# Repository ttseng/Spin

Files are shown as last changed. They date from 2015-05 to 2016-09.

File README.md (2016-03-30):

# Spin Turntable System

Find all the design files for building your own Spin turntable (http://spin.media.mit.edu/) here.

## Arduino

This folder contains the SoftModem library needed for the spin.ino Arduino sketch.  The spin sketch should be uploaded to the Arduino Uno running Spin.

## CAD

If you are building a turntable and have access to a laser cutter with a bed larger than 12", build the DEFAULT turntable.  If you have a smaller laser cutter that cannot cut material larger than 12", build the Modified 12-inch turntable design.  Both designs have the same exact footprint (13"), but the modified 12-inch turntable has smaller laser cut parts and has an additional set of three 3D printed feet.

Each contains three subfolders: _3D Print_, _Laser Cut_, and _Solidworks_.  Building your own Spin turntable requires laser cutting parts in 3/16" and 1/8" acrylic, which can be found in the _Laser Cut_ folder in Illustrator, Corel Draw, and DXF formats.  Additionally, you'll need to 3D print a gear (motor_gear.STL), which can be found in the _3D print_ folder.  Optionally, you can 3D print your own iOS device dock (which can be used with an iPhone 4/5/6 or iPad/iPad mini).  If you are building the modified turntable, you will also need to 3D print three feet.  

You can find all the original CAD files in the _Solidworks_ folder.

## PCB

The Eagle files and libraries for the Spin shield are located here.  You can purchase the shield directly from OSH Park: https://oshpark.com/profiles/scientiffic

## Processing

This is an optional Processing sketch for controlling the Spin turntable with your computer via a USB connection to the Uno.  You can use this to debug your turntable or to just control it without using an iOS device.

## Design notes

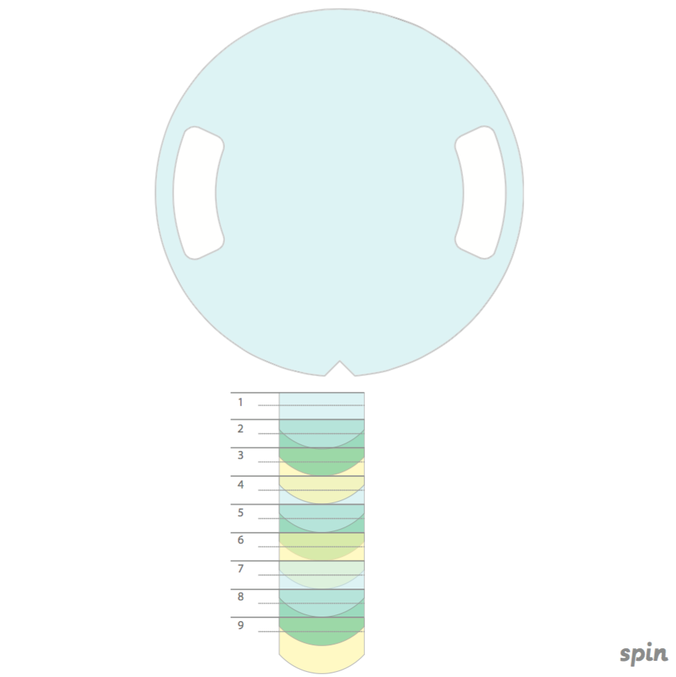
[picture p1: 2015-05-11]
Mat/mat.png

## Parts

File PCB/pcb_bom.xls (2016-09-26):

Item | Vendor | Quantity | Part Number | Total Price
Easy Drive Stepper Motor Driver | Sparkfun | 1 | ROB-12779 (https://www.sparkfun.com/products/12779) | 14.95
Blue LEDs 1206 SMD | Sparkfun | 1 (strip of 25) | PRT-12620 (https://www.sparkfun.com/products/12620) | 2.95
Male headers | Sparkfun | 2 | PRT-00116 (https://www.sparkfun.com/products/116) | 3
Female headers | Digikey | 1 | S5440-ND (http://www.digikey.com/product-detail/en/PPTC041LGBN-RC/S5440-ND/775898) | 0.63
3.5mm audio jack | Digikey | 1 | CP-43514-ND (http://www.digikey.com/product-search/en?KeyWords=CP-43514-ND&WT.z_header=search_go) | 1.18
100 Ω resistor 1206 SMD | Digikey | 4 | 311-100FRCT-ND (http://www.digikey.com/product-detail/en/0/311-100FRCT-ND) | 0.45
1 kΩ resistor 1206 SMD | Digikey | 2 | P1.0KECT-ND (http://www.digikey.com/product-detail/en/ERJ-8GEYJ102V/P1.0KECT-ND/203248) | 0.09
10 kΩ resistor 1206 SMD | Digikey | 1 | 311-10.0KFRCT-ND (http://www.digikey.com/product-detail/en/RC1206FR-0710KL/311-10.0KFRCT-ND/731430) | 0.09
0.22 µF 1206 capacitor | Digikey | 1 | 399-1251-1-ND (http://www.digikey.com/product-search/en?KeyWords=399-1251-1-ND&WT.z_header=search_go) | 0.17
 |  |  |  | Total: $23.51

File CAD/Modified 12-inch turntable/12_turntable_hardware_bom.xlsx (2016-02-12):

Item | Vendor | Quantity | Part Number | Total Price
Specialized Parts
Turntable | McMaster | 1 | 18635A52 (http://www.mcmaster.com/#18635a52/=vv6p0h) | 37.03
M3 Heat-Set Inserts | McMaster | 1 (pack of 100) | 94180A331 (http://www.mcmaster.com/#94180a331/=wy5p3e) | 12.3
Acrylic
3/16" acrylic (total area of 24" x 12") | Tap Plastics | 1 | 3/16" acrylic (http://www.tapplastics.com/product/plastics/cut_to_size_plastic/acrylic_sheets_clear/508) | 13.3
⅛" white acrylic (12"x12") | Tap Plastics | 1 | 1/8" acrylic (http://www.tapplastics.com/product/plastics/cut_to_size_plastic/acrylic_sheets_color/341) | 10
Misc Electronics
Stepper Motor | Sparkfun | 1 | ROB-09238 (https://www.sparkfun.com/products/9238) | 14.95
Arduino Uno | Sparkfun | 1 | DEV-11021 (https://www.sparkfun.com/products/11021) | 24.95
12VDC Wall Adapter | Sparkfun | 1 | TOL-09442 (https://www.sparkfun.com/products/9442) | 5.94
M3 Standoffs | Digikey | 4 | 952-2189-ND (http://www.digikey.com/product-search/en?KeyWords=952-2189-ND&WT.z_header=search_go) | 2.24
3.5mm Audio Cable | Amazon | 1 | Audio Cable (http://www.amazon.com/EMEMO®-Quality-Auxilliary-Straight-Generation/dp/B00JJVPUE2) | 5.99
Fasteners
M3 set screw (4mm length) |  | 2
M3 machine screws (10mm length) |  | 18
M3 nuts |  | 7
¼-20 machine screws (0.625" length) |  | 9
¼-20 nuts |  | 9
5/16 machine screws (2.5" length) |  | 3
5/16 nuts |  | 3
 |  |  |  | Total: $126.70 + ~ $10 for fasteners

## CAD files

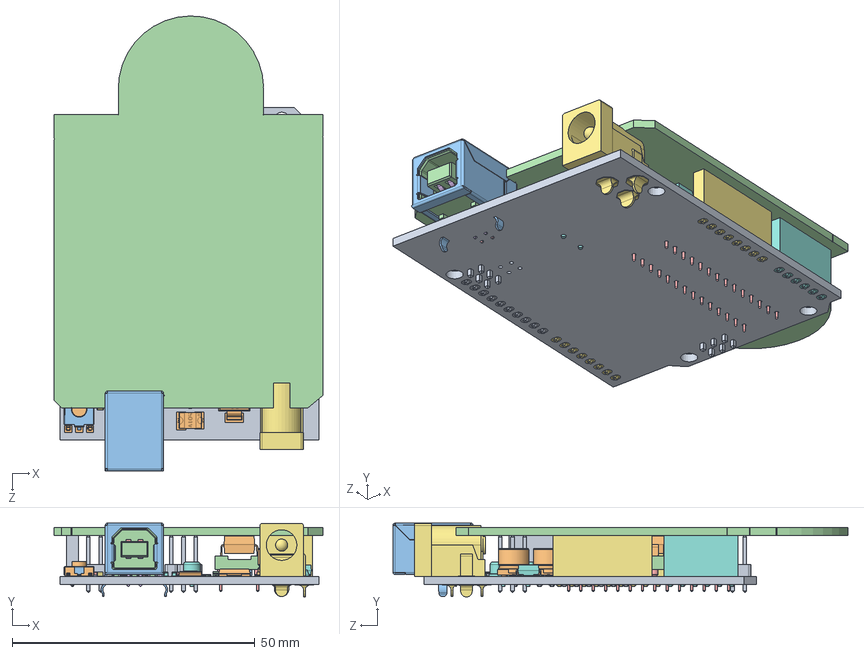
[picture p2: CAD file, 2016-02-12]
CAD/Modified 12-inch turntable/Solidworks/arduino-assembly.SLDASM
55.4 x 15.2 x 93.8 mm
unoboard blue
47uf CAP Dcase x 2
USB SHELL
USB core
usb top contact x 2
usb btm contact x 2
power jack
crystal
2pin_header__02 x 6
nano - reg
led x 4
dip28
dip socket pin x 28
atmega16u2
8 PORT HEADER x 2
6 PORT HEADER
10 PORT HEADER
ATMEL328P
102 RESISTOR PACK x 2
103 RESISTOR PACK
220 RESISTOR PACK
16mhz crystal - measured
PADS001
603 cap on pad x 8
ssot3
mf-msmf050-2
lmv358
lp2985dgkr
cd1206 diode x 2
603 resistor
blm21
m7 diode
MLC0603 x 2
RESET CORE
RESET
PCB

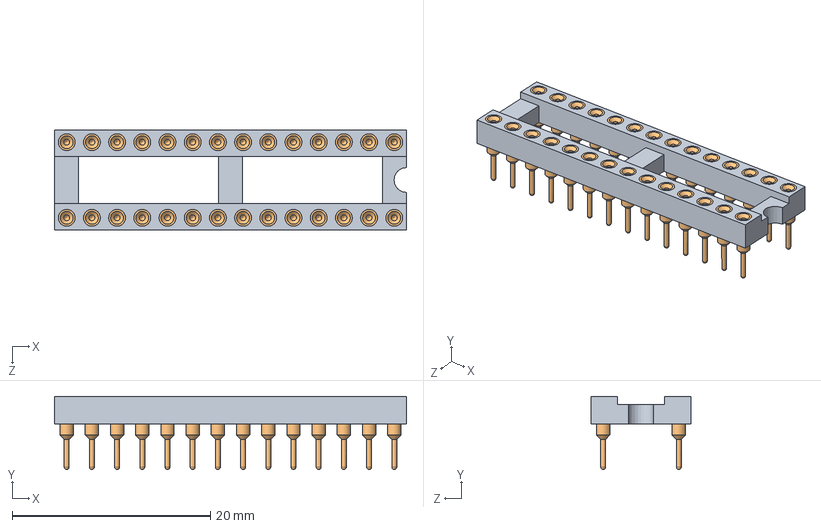
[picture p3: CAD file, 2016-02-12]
CAD/Modified 12-inch turntable/Solidworks/dip28.SLDASM
35.5 x 7.37 x 10.1 mm
dip28
dip socket pin x 28

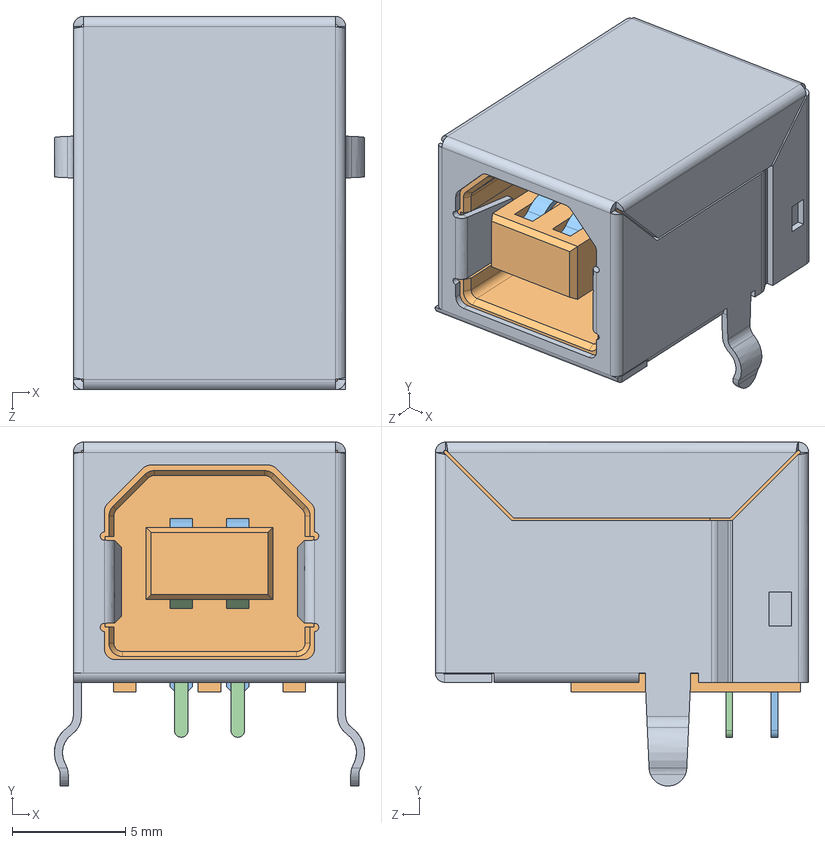
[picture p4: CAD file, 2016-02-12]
CAD/Modified 12-inch turntable/Solidworks/USB type b.SLDPRT.SLDASM
13.7 x 15.2 x 16.5 mm
USB SHELL
USB core
usb top contact x 2
usb btm contact x 2

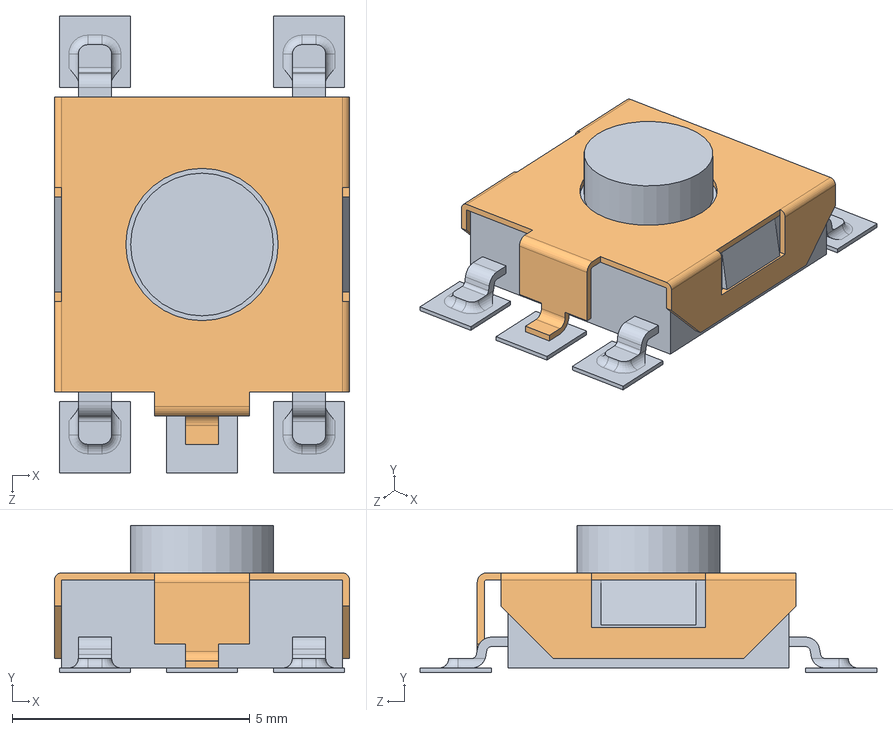
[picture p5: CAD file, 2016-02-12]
CAD/Modified 12-inch turntable/Solidworks/RESET BUTTON.SLDASM
6.20 x 3.10 x 9.60 mm
RESET CORE
RESET

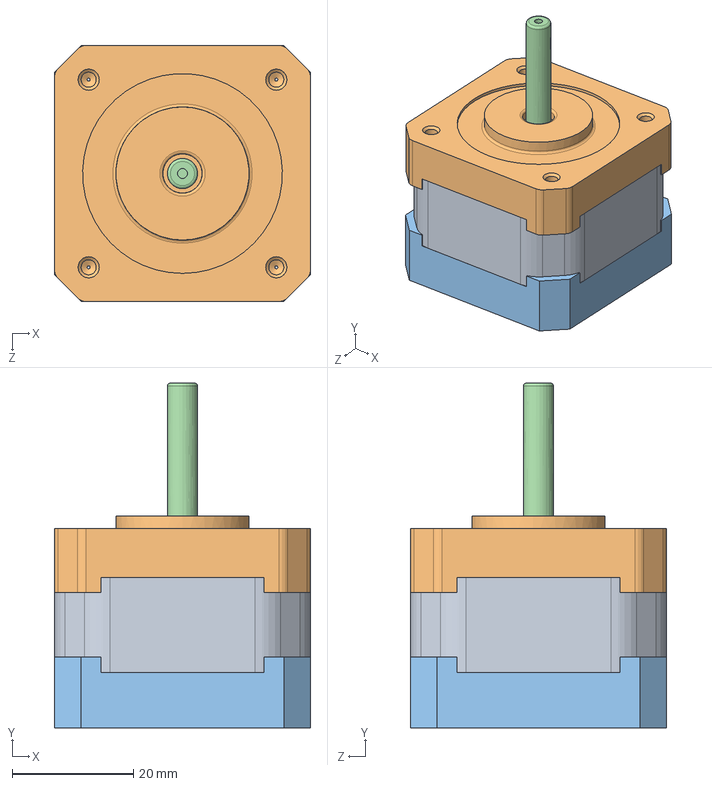
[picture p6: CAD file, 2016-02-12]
CAD/Modified 12-inch turntable/Solidworks/SparkFun Stepper Motor Assembly.SLDASM
42.3 x 57.0 x 42.3 mm
NEMA 17 Stepper Motor Middle
NEMA 17 Stepper Motor Top
NEMA 17 Stepper Motor Bottom
NEMA 17 Stepper Motor Shaft
pan cross head_am x 4

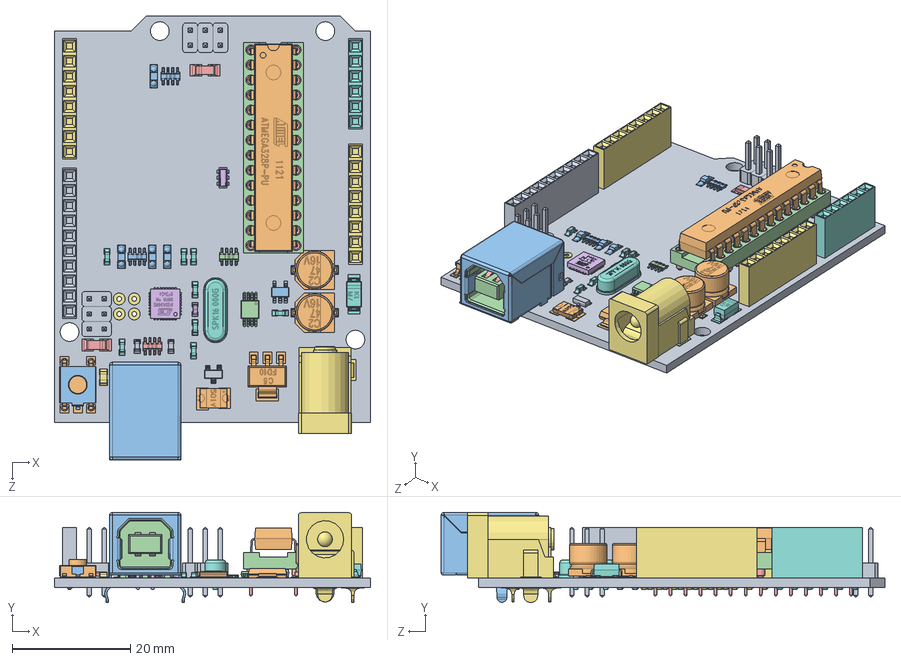
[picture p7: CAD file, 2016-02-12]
CAD/DEFAULT turntable/Solidworks/arduino uno.SLDASM
53.3 x 15.2 x 74.9 mm
unoboard blue
47uf CAP Dcase x 2
USB SHELL
USB core
usb top contact x 2
usb btm contact x 2
power jack
crystal
2pin_header__02 x 6
nano - reg
led x 4
dip28
dip socket pin x 28
atmega16u2
8 PORT HEADER x 2
6 PORT HEADER
10 PORT HEADER
ATMEL328P
102 RESISTOR PACK x 2
103 RESISTOR PACK
220 RESISTOR PACK
16mhz crystal - measured
PADS001
603 cap on pad x 8
ssot3
mf-msmf050-2
lmv358
lp2985dgkr
cd1206 diode x 2
603 resistor
blm21
m7 diode
MLC0603 x 2
RESET CORE
RESET

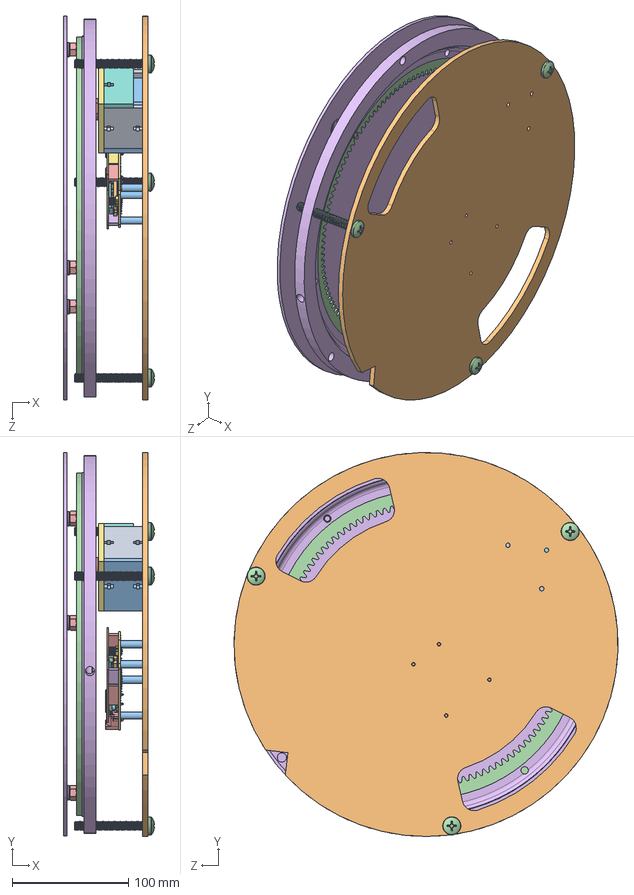
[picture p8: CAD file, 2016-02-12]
CAD/DEFAULT turntable/Solidworks/turntable_assembly.SLDASM
78.2 x 330.2 x 330.2 mm
NEMA 17 Stepper Motor Middle
NEMA 17 Stepper Motor Top
NEMA 17 Stepper Motor Bottom
NEMA 17 Stepper Motor Shaft
pan cross head_am x 4
turntable
stepper_case_top
stepper_case_side_1
stepper_case_side_2 x 2
base
stepper_case_side_3
outer_gear
motor_gear_2
unoboard blue
47uf CAP Dcase x 2
USB SHELL
USB core
usb top contact x 2
usb btm contact x 2
power jack
crystal
2pin_header__02 x 6
nano - reg
led x 4
dip28
dip socket pin x 28
atmega16u2
8 PORT HEADER x 2
6 PORT HEADER
10 PORT HEADER
ATMEL328P
102 RESISTOR PACK x 2
103 RESISTOR PACK
220 RESISTOR PACK
16mhz crystal - measured
PADS001
603 cap on pad x 8
ssot3
mf-msmf050-2
lmv358
lp2985dgkr
cd1206 diode x 2
603 resistor
blm21
m7 diode
MLC0603 x 2
RESET CORE
RESET
PCB
standoff x 4
91772A634 x 3
90499A029 x 3
94836A420 x 3

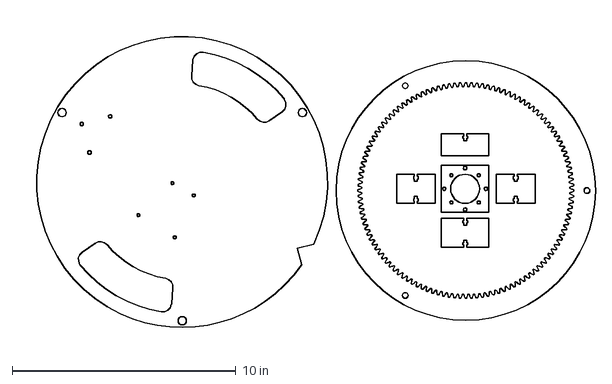
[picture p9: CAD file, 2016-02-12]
CAD/DEFAULT turntable/Laser Cut/DXF/3_16_acrylic.dxf
25.9 x 14.6 in

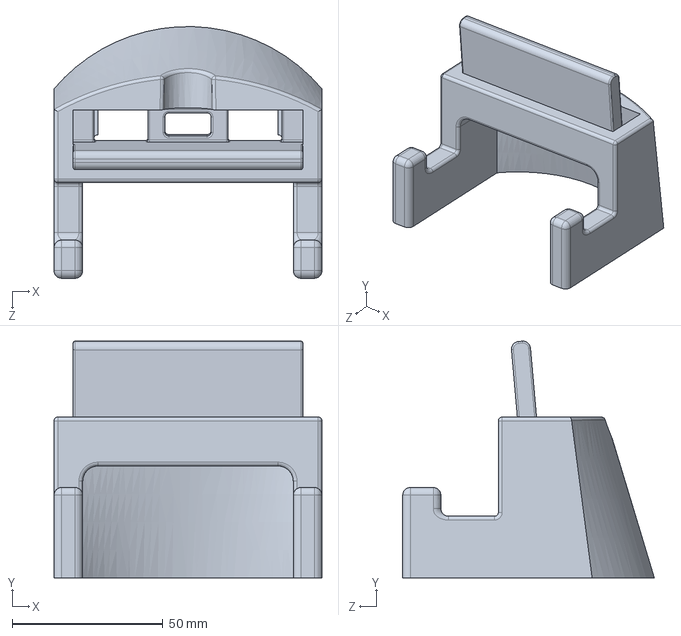
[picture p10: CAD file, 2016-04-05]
CAD/DEFAULT turntable/Solidworks/ios_dock.SLDPRT
88.9 x 78.5 x 83.5 mm

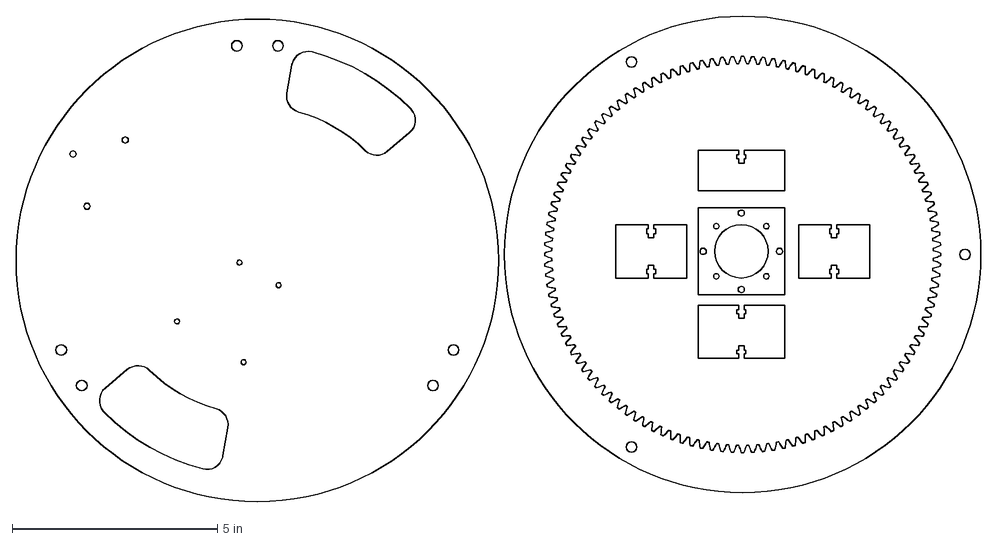
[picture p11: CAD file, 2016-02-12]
CAD/Modified 12-inch turntable/Laser Cut/DXF/3_16_acrylic.dxf
23.5 x 11.8 in

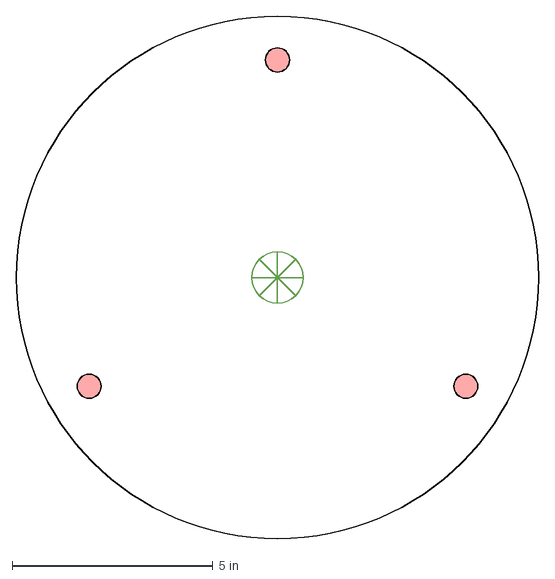
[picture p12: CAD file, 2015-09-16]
CAD/DEFAULT turntable/Laser Cut/DXF/1_8_acrylic.dxf
13.0 x 13.0 in

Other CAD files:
CAD/DEFAULT turntable/Solidworks/USB type b.SLDPRT.SLDASM
CAD/DEFAULT turntable/Solidworks/dip28.SLDASM
CAD/DEFAULT turntable/Solidworks/RESET BUTTON.SLDASM
CAD/DEFAULT turntable/Solidworks/SparkFun Stepper Motor Assembly.SLDASM
CAD/DEFAULT turntable/Solidworks/arduino-assembly.SLDASM
CAD/Modified 12-inch turntable/Solidworks/arduino uno.SLDASM
CAD/DEFAULT turntable/3D Print/ios_dock.STL
CAD/DEFAULT turntable/3D Print/motor_gear_2.STL
CAD/DEFAULT turntable/Solidworks/10 PORT HEADER.SLDPRT
CAD/DEFAULT turntable/Solidworks/102 RESISTOR PACK.SLDPRT
CAD/DEFAULT turntable/Solidworks/103 RESISTOR PACK.SLDPRT
CAD/DEFAULT turntable/Solidworks/16mhz crystal - measured.SLDPRT
CAD/DEFAULT turntable/Solidworks/220 RESISTOR PACK.SLDPRT
CAD/DEFAULT turntable/Solidworks/2pin_header__02.sldprt
CAD/DEFAULT turntable/Solidworks/47uf CAP Dcase.SLDPRT
CAD/DEFAULT turntable/Solidworks/6 PORT HEADER.SLDPRT
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

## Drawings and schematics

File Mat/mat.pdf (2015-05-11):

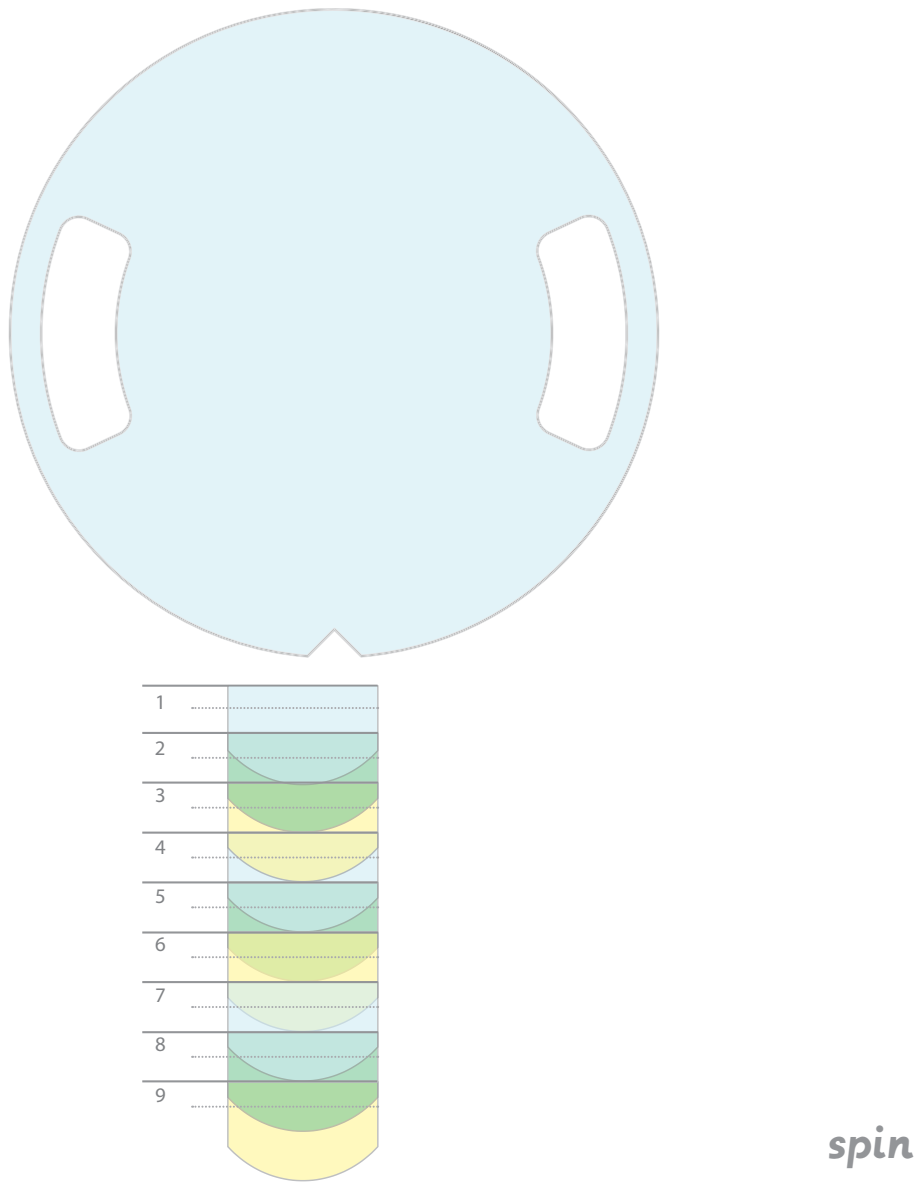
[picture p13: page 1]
spin

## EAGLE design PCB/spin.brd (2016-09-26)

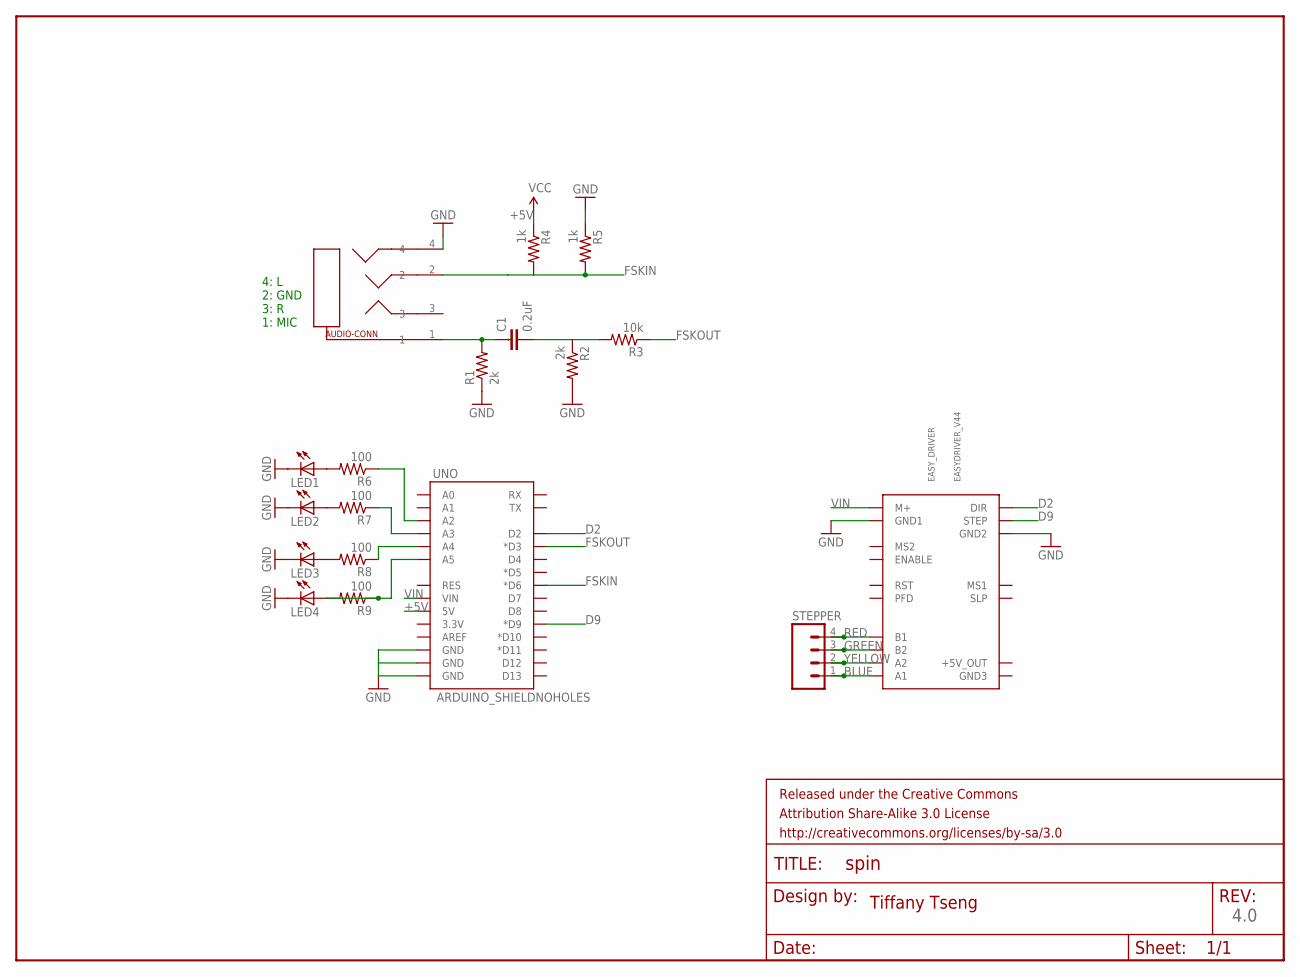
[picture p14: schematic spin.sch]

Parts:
C1: 0.2uF; 1206
EASY_DRIVER: EASYDRIVER_V44
FRAME1: FRAME-LETTER; CREATIVE_COMMONS
LED1, LED2, LED3, LED4: LED1206; 1206
R1, R2: 2k; R1206
R3: 10k; R1206
R4, R5: 1k; R1206
R6, R7, R8, R9: 100; R1206
STEPPER: M04PTH; 1X04
U$1: SJ-43514
UNO: ARDUINO_SHIELDNOHOLES; DUEMILANOVE_SHIELD_NOHOLES

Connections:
1: C1.1, R1.2, U$1.1
+5V: R4.1, UNO.5V
BLUE: EASY_DRIVER.A1, STEPPER.1
D2: EASY_DRIVER.DIR, UNO.D2
D9: EASY_DRIVER.STEP, UNO.D9 (*D9)
FSKIN: R4.2, R5.2, U$1.2, UNO.D6 (*D6)
FSKOUT: R3.1, UNO.D3 (*D3)
GND: EASY_DRIVER.GND1, EASY_DRIVER.GND2, LED1.2 (C), LED2.2 (C), LED3.2 (C), LED4.2 (C), R1.1, R2.2, R5.1, U$1.4, UNO.GND@0 (GND), UNO.GND@1 (GND), UNO.GND@2 (GND)
GREEN: EASY_DRIVER.B2, STEPPER.3
unnamed: C1.2, R2.1, R3.2
unnamed: R9.1, UNO.A5
unnamed: LED1.1 (A), R6.2
unnamed: LED2.1 (A), R7.2
unnamed: R8.1, UNO.A4
unnamed: LED3.1 (A), R8.2
unnamed: R7.1, UNO.A3
unnamed: LED4.1 (A), R9.2
unnamed: R6.1, UNO.A2
RED: EASY_DRIVER.B1, STEPPER.4
VIN: EASY_DRIVER.M+, UNO.VIN
YELLOW: EASY_DRIVER.A2, STEPPER.2

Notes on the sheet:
4: L 2: GND 3: R 1: MIC
4.0
Tiffany Tseng

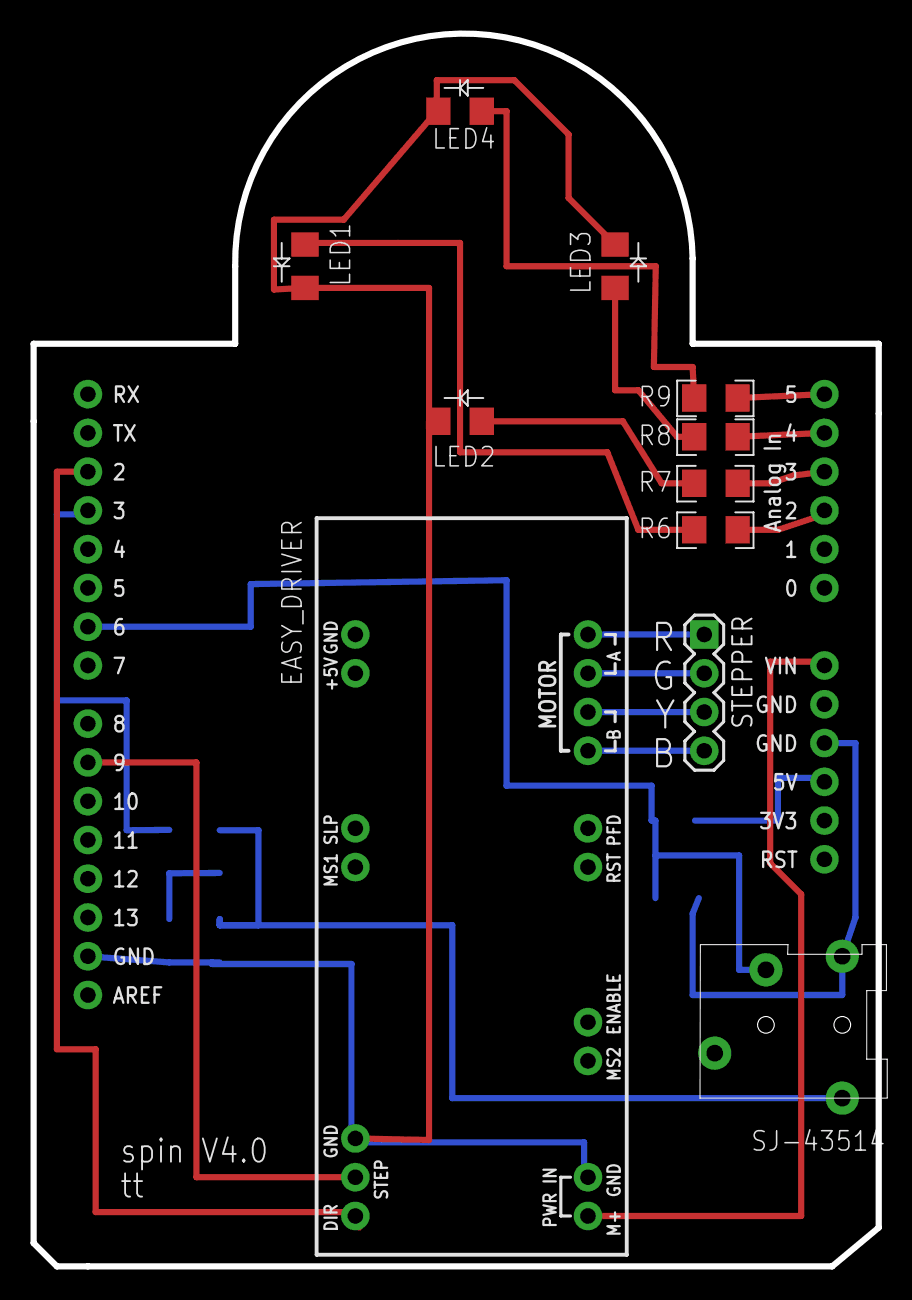
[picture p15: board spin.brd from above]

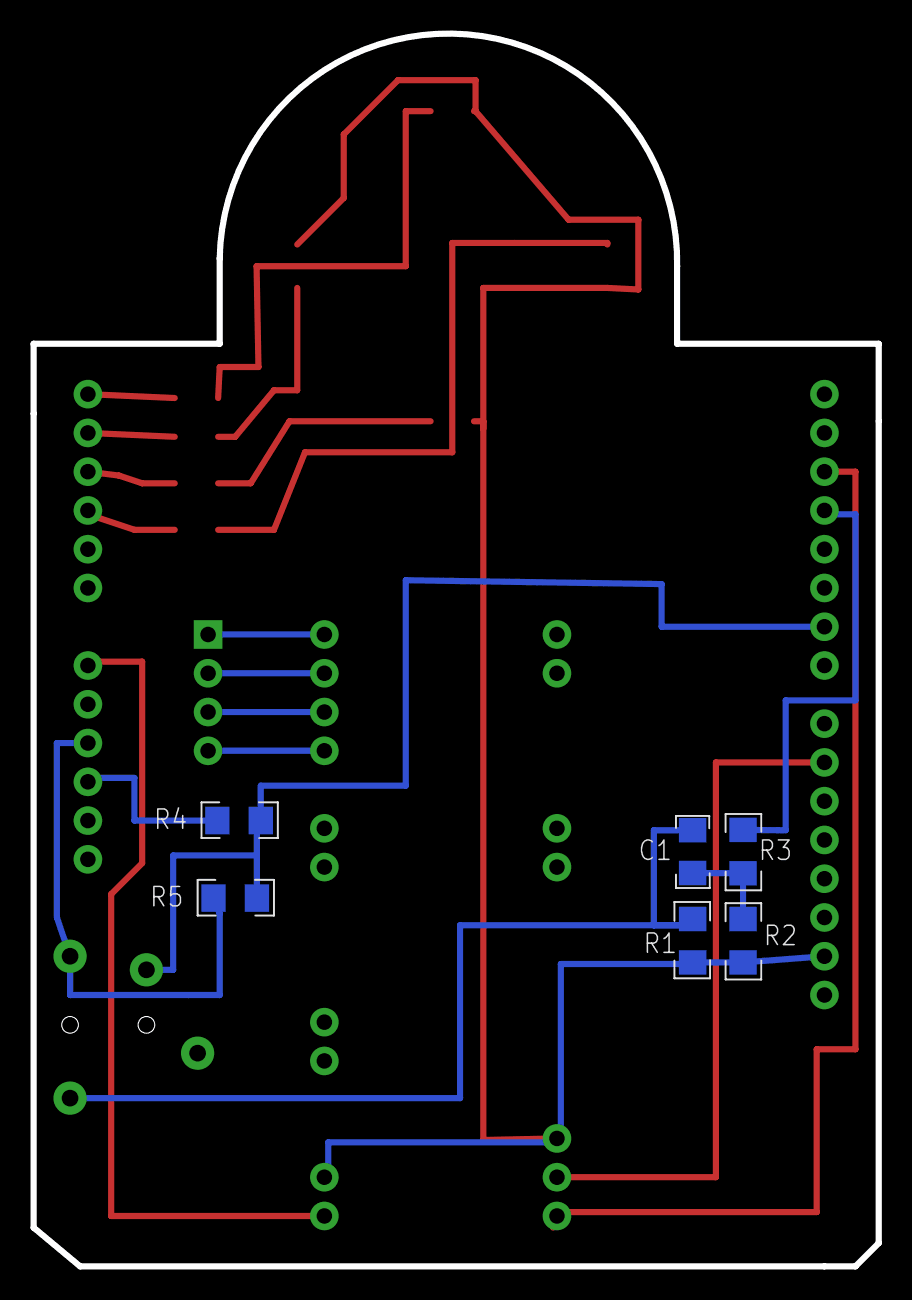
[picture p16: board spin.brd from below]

Board: 2 copper layers, 55.4 x 80.8 mm, 19 parts (6 on the bottom side), 21 nets.

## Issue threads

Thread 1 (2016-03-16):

Trouble Connecting with iPad

PCswanson, 2016-03-16:
The spin is able to be controlled using the Processing sketch. When I plug it into the iPad and run through the setup sequence, it moves the motor a short distance back and forth 4 times and then gives me an "Unable to connect to turntable" error message.

I switched from a Sparkfun Redboard to an actual Arduino Uno, and now it moves a short distance in one direction 4 times (instead of back and forth) and then gives me the same error message.

ttseng, 2016-03-16:
Are you using the recommended 4-pin 3.5mm audio cable?

http://www.amazon.com/Supertech%C2%AE3-5mm-Premium-Compatible-Smartphones-computers/dp/B00PLTXJIU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

It needs to be 4 pin (not a standard 3 pin cable).  If you are using a 4-pin cable, please check that the mic lines of both ends are connected.  You can do this with a multimeter (the mic line is the pin closest to the barrel).

Also, please double check when you go into settings on your iPad that under Spin, you allow the app to access the microphone.

Let me know if this resolves the issue!

PCswanson, 2016-03-18:
I have the recommended cable, and I double checked and the microphone is turned on. Any other suggestions? Thanks!

ttseng, 2016-03-18:
Did you assemble your own PCB from scratch?  I would double check connections to the MIC line of the audio jack:

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

Do you mind sharing more information about your device as well (iPad type, OS, etc.)?

PCswanson, 2016-03-18:
I've tried it on an iPad3 and an iPhone5s. I purchased the PCB and soldered the components - I'm going to check the connections around the mic when I get back to my lab this afternoon. Thanks!

PCswanson, 2016-03-23:
Here's an update - the problem I started with was solved and I'll blame my own inexperience with surface mount soldering. Specifically the R3 resistor was non functional. I must have done something to it when placing it. I couldn't get a reading at all with a multi tester. Replaced it and I could connect with both the iPad and iPhone. Your suggestion to work back and check from the mic input was very helpful - thanks!

New problem: In case you haven't figured it out, I'm the one you've been tweeting with. The motor doesn't seem to be getting enough power. I've fiddled with the little pot on the motor controller board but it hasn't made a difference. Changing the motor_speed variable from .2 to .1 makes the motor rotate the full 240deg, but now it is out of sync with the app.  Any ideas?  Thanks in advance.

ttseng, 2016-03-23:
Please ensure that you are using the recommended 12V 600mA power supply: https://www.sparkfun.com/products/9442

It will not have enough power from USB power alone.

I would also check that the EasyDriver board motor PWR IN pins are getting the expected 12V.

PCswanson, 2016-03-23:
That was it - I used a 5V supply instead of the 12V one that I purchased for the Spin. It is now fully functional. Thanks!

ttseng, 2016-03-23:
Great to hear!

Closed 2016-03-23.

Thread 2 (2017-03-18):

Spin App won't connect

dhammy0110, 2017-03-18:
I am building this using a DIY Easy Driver shield and have it breadboarded at the moment. Everything seems to be wired correctly, using the 'patched' Softmodem library, the multimeter reads the pins from the TRRS iphone cable correctly, that circuit seems to be correct as well.

When I click begin setup > begin > next >
It says "connecting to turntable...", spins the stepper motor around a few times, but then the iOS app says "unable to connect turntable!".

I've gone over everything for days and can't figure out why this won't work. Any ideas?

Thanks!

- Damon, aka Semiconducted

ttseng, 2017-03-18:
Hi, there!  I'll do my best to help debug.  Let's figure out if it's a hardware issue with the turntable itself first.  Are you able to successfully run the stepper motor via USB from the Arduino with the Processing sketch here? http://spin.media.mit.edu/build#program_arduino

dhammy0110, 2017-03-18:
Thanks for your response!

Yes, the processing sketch works. I had to crank up the motor_speed to 1 and multiply rotAmt by 10 to see any effect, but yes.
The iOS app throws the error, right after the stepper does its little dance. So it seems the SoftModem is issuing commands, but the board is not sending or the app is not recognizing the feedback? I see numbers popping in the Serial Monitor, but not sure what to look for or how to troubleshoot.

Also, is it normal for the stepper motor to be loud and vibratey? Reducing vibration and noise would be a plus, as my end goal is to customize Spin for 3D scanning. If you know anyone who’s taken that direction, let me know!
I started investigating replacing the motor control methods with the AccelStepper library to hopefully make it smoother and more extensible, but software might not actually be what’s cause that other issue.

Thanks!

- Damon
____
Damon Hamm
www.semiconducted.com
d@damonhamm.com
www.linkedin.com/in/damonhamm

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

ttseng, 2017-03-18:
After the app sends a signal to the turntable, it expects to receive a signal back on the mic line of the audio cable.  I'm using the ring closest to the base of the audio cable for the mic line, so you might try ensuring that both ends of the 4-pin audio jack are connected at that ring (I have experienced purchasing faulty 4 pin audio cables in the past).  It's also possible that the Arduino is sending a signal via the mic line back to the phone but it's not being amplified enough for the phone to detect.  I don't know if having a different motor driver might affect the signal, but you could try playing around with R2 and R3 to ensure the signal is strong enough.

If you have a custom version of the Easy Driver, it's important to ensure that it's capable of microstepping if you care about volume  I've tried using other motor drivers (TB6612FNG in particular) and it was extremely loud since it couldn't microstep.

Let me know if that helps!

dhammy0110, 2017-03-20:
Still no luck changing the resistors to the original SoftModem circuit below and also changed R2 and R3 both to 4.7k, to no avail.
I’m curious, why is your schematic for this circuit different than the creators'? What are the advantages?

I’m not sure how exactly to test or if I should change the resistors up or down. My multimeter shows a signal coming through all the way to the ring (it is a little exposed), though the app does not respond. In the meantime I ordered the exact cable you specified from Amazon.com in the hopes it is my cable.

Thanks!

- Damon

 https://raw.githubusercontent.com/arms22/SoftModem/master/extras/schematic.png <https://raw.githubusercontent.com/arms22/SoftModem/master/extras/schematic.png>

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

dhammy0110, 2017-05-13:
Hey Tiffany, Damon Hamm here just following up with an update.I was able to track down what was causing the problem and of course it was the last place I looked - a bad motor power supply! It was registering correct voltage and rated for 3A, but when running the motor the motor was insanely choppy and loud. I of course thought it was the motor driver chip, something else in the circuit, yada yada. It was only when I used an oscilloscope to analyze the audio signals that I discovered the noise that obliterated everything else. I swapped out the motor power supply and suddenly everything worked perfectly.Thanks again for sharing this project! I plan to post my DIY shield setup and arduino code mods when finished. 
- Damon HammP.S. I also noticed you also are a UXer! Since the MIT media lab wouldn’t have me ☹️, I did my masters at Carnegie Mellon 😀.www.damonhamm.comwww.semiconducted.comd@damonhamm.com

On 2017-Mar-18, at 3:08 AM, Tiffany Tseng <notifications@github.com> wrote:After the app sends a signal to the turntable, it expects to receive a signal back on the mic line of the audio cable.  I'm using the ring closest to the base of the audio cable for the mic line, so you might try ensuring that both ends of the 4-pin audio jack are connected at that ring (I have experienced purchasing faulty 4 pin audio cables in the past).  It's also possible that the Arduino is sending a signal via the mic line back to the phone but it's not being amplified enough for the phone to detect.  I don't know if having a different motor driver might affect the signal, but you could try playing around with R2 and R3 to ensure the signal is strong enough.If you have a custom version of the Easy Driver, it's important to ensure that it's capable of microstepping if you care about volume  I've tried using other motor drivers (TB6612FNG in particular) and it was extremely loud since it couldn't microstep.Let me know if that helps!—You are receiving this because you authored the thread.Reply to this email directly, view it on GitHub, or mute the thread.

{"api_version":"1.0","publisher":{"api_key":"05dde50f1d1a384dd78767c55493e4bb","name":"GitHub"},"entity":{"external_key":"github/ttseng/Spin","title":"ttseng/Spin","subtitle":"GitHub repository","main_image_url":"<a href="https://cloud.githubusercontent.com/assets/143418/17495839/a5054eac-5d88-11e6-95fc-7290892c7bb5.png" class="">https://cloud.githubusercontent.com/assets/143418/17495839/a5054eac-5d88-11e6-95fc-7290892c7bb5.png</a>","avatar_image_url":"<a href="https://cloud.githubusercontent.com/assets/143418/15842166/7c72db34-2c0b-11e6-9aed-b52498112777.png" class="">https://cloud.githubusercontent.com/assets/143418/15842166/7c72db34-2c0b-11e6-9aed-b52498112777.png</a>","action":{"name":"Open in GitHub","url":"<a href="https://github.com/ttseng/Spin" class="">https://github.com/ttseng/Spin</a>"}},"updates":{"snippets":[{"icon":"PERSON","message":"@ttseng in #2: After the app sends a signal to the turntable, it expects to receive a signal back on the mic line of the audio cable.  I'm using the ring closest to the base of the audio cable for the mic line, so you might try ensuring that both ends of the 4-pin audio jack are connected at that ring (I have experienced purchasing faulty 4 pin audio cables in the past).  It's also possible that the Arduino is sending a signal via the mic line back to the phone but it's not being amplified enough for the phone to detect.  I don't know if having a different motor driver might affect the signal, but you could try playing around with R2 and R3 to ensure the signal is strong enough.\r\n\r\nIf you have a custom version of the Easy Driver, it's important to ensure that it's capable of microstepping if you care about volume  I've tried using other motor drivers (TB6612FNG in particular) and it was extremely loud since it couldn't microstep.\r\n\r\nLet me know if that helps!"}],"action":{"name":"View Issue","url":"<a href="https://github.com/ttseng/Spin/issues/2#issuecomment-287521926" class="">https://github.com/ttseng/Spin/issues/2#issuecomment-287521926</a>"}}}

ttseng, 2017-05-16:
@dhammy0110 that's great to hear!  excited to see your modifications to Spin!

Closed 2017-05-16.

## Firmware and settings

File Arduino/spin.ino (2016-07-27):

/*
  Spin
  Default sketch for controlling the Spin turtntable using the Spin iOS app
  Also includes debugging functionality to use with the Processing Sketch
  Find additional documentation at spin.media.mit.edu/build
  Stepper Motor Code Modified from BILDR: http://bildr.org/2011/06/easydriver/
  
  Author: Tiffany Tseng  
  Last Updated: 07/26/2016
  Added FSKModem responses for Android app
  
*/

#include <SoftModem.h>
#include <ctype.h>

#define DIR_PIN 2
#define STEP_PIN 9
#define BTN_PIN 12

#define LED_PIN 13
#define LED_PIN_1 A2
#define LED_PIN_2 A3
#define LED_PIN_3 A4
#define LED_PIN_4 A5


SoftModem modem;

boolean rotating = false;
boolean cancelled = false;
int numRotations = 15;// should be 15
int currentRotation = 0;
char val;
float rotAmt = 240; // the number of degrees the stepper should turn for each increment
float motor_speed = 0.2;

int buttonState = HIGH;  
int lastButtonState = LOW;
long lastDebounceTime = 0;
long debounceDelay = 20;
boolean spinCreated = false;

void setup() { 
  pinMode(DIR_PIN, OUTPUT); 
  pinMode(STEP_PIN, OUTPUT); 
  pinMode(LED_PIN, OUTPUT);
  pinMode(LED_PIN_1, OUTPUT);
  pinMode(LED_PIN_2, OUTPUT);
  pinMode(LED_PIN_3, OUTPUT);
  pinMode(LED_PIN_4, OUTPUT);
  pinMode(BTN_PIN, INPUT_PULLUP);
  Serial.begin(9600);
  modem.begin();
} 

void loop(){

  if(rotating == false){
    // keep two of the LED lights on when the turntable is powered
    digitalWrite(LED_PIN_3, HIGH);
    digitalWrite(LED_PIN_1, HIGH);
  }

  if(modem.available ()) {
    // RECEIVED SIGNAL FROM IPHONE 
    int input = modem.read ();
    Serial.println(input);

    if(input == 253  || input == 93){
      // begin spin - flash LEDs
      Serial.println(" start ");
      modem.write(0xFC); // send confirmation signal to app (252)
      flashLEDsOnce();
      currentRotation = 0;
      rotating = true;
      cancelled = false;
      delay(1000);
    }else if(input==251 || input == 91){
      // stop arduino
      rotating = false;
      cancelled = true;
      spinCreated = false;
      currentRotation = 0;
      Serial.println(" stop - writing stop signal");
      modem.write(0xFE); // 254
    }else if(input == 234 || input == 74){
      // setup signal received (for one-time setup when user first downloads app)
      flashLEDsOnce();
      modem.write(0xEC);
      rotateDeg(-rotAmt/2, motor_speed);
      rotateDeg(rotAmt/2, motor_speed);
    }else if(input == 255){
      // spin has been created -> (used for enabling remote shutter button)
      spinCreated = true;
    }
  }
  
  if(rotating && !cancelled && currentRotation < numRotations){
//    Serial.println(currentRotation+1);
    singleRotation();
    currentRotation++;
  }else{
    rotating = false;
    cancelled = true;
  }
  
  if(Serial.available()){
    // SIGNAL RECEIVED FROM SERIAL MONITOR / PROCESSING
      val = Serial.read();
      // read serial character from the serial monitor and send to arduino  
      // blink LED to show that signal was sent to iPhone
      ledsOn();
      delay(2);
      ledsOff();

      // KEYBOARD INPUT FOR DEBUGGING THROUGH PROCESSING
      if(val=='L'){
        // nudge the motor CW 
        ledsOn();
        rotateDeg(-rotAmt, motor_speed);
        ledsOff();
      }else if(val=='R'){
        // nudge the motor CCW 
        ledsOn();
        rotateDeg(rotAmt, motor_speed);
        ledsOff();    
      }else if(val=='S'){
        // do a full 360 spin, stopping 15 times
        takePhoto();
        for(int i = 0; i<numRotations; i++){
          ledsOn();
          // move the motor
          rotateDeg(-rotAmt, motor_speed);
          ledsOff();
          if(i!=numRotations-1){
            takePhoto();
          }
        }
        flashLEDs();
      }else if(val=='T'){
        // do a full 360 spin, no stopping
        ledsOn();
        rotateDeg(-3600.0, motor_speed);
        ledsOff();
      }else if(val=='P'){
        // take a photo
        takePhoto();
      }
    }
    
 // EASY BUTTON STUFF
  
  int reading = digitalRead(BTN_PIN);
  if(reading != lastButtonState){
  
    lastDebounceTime = millis();
  }
  
  if ((millis() - lastDebounceTime) > debounceDelay) {
    // whatever the reading is at, it's been there for longer
    // than the debounce delay, so take it as the actual current state:

    // if the button state has changed:
    if (reading != buttonState) {
      buttonState = reading;
  
      // only toggle the LED if the new button state is HIGH
      if (buttonState == HIGH && spinCreated) {
          Serial.println("write start to app");
           modem.write(0xFC); // send confirmation signal to app
           flashLEDsOnce();
           currentRotation = 0;
           rotating = true;
           cancelled = false;
           delay(1000);
      }
    }
  }
  
  lastButtonState = reading;

}

void singleRotation(){
  rotating = true;
  ledsOn();
  rotateDeg(-rotAmt, motor_speed);
  ledsOff();
  takePhoto();
}

void takePhoto(){
  // time it takes to capture photo and add imageview in app
  delay(1950);
}

void rotate(int steps, float speed){ 
  //rotate a specific number of microsteps (8 microsteps per step) - (negative for reverse movement)
  //speed is any number from .01 -> 1 with 1 being fastest - Slower is stronger
  int dir = (steps > 0)? HIGH:LOW;
  steps = abs(steps);

  digitalWrite(DIR_PIN,dir); 

  float usDelay = (1/speed) * 70;

  for(int i=0; i < steps; i++){ 
    digitalWrite(STEP_PIN, HIGH); 
    delayMicroseconds(usDelay); 

    digitalWrite(STEP_PIN, LOW); 
    delayMicroseconds(usDelay); 
  } 
} 

void rotateDeg(float deg, float speed){ 
  //rotate a specific number of degrees (negitive for reverse movement)
  //speed is any number from .01 -> 1 with 1 being fastest - Slower is stronger
  int dir = (deg > 0)? HIGH:LOW;
  digitalWrite(DIR_PIN,dir); 

  int steps = abs(deg)*(1/0.225);
  float usDelay = (1/speed) * 70;

  for(int i=0; i < steps; i++){ 
    digitalWrite(STEP_PIN, HIGH); 
    delayMicroseconds(usDelay); 

    digitalWrite(STEP_PIN, LOW); 
    delayMicroseconds(usDelay); 
  } 
}

void ledsOn(){
  digitalWrite(LED_PIN_1, HIGH);
  digitalWrite(LED_PIN_2, HIGH);
  digitalWrite(LED_PIN_3, HIGH);
  digitalWrite(LED_PIN_4, HIGH);
}

void ledsOff(){
  digitalWrite(LED_PIN_1, LOW);
  digitalWrite(LED_PIN_2, LOW);
  digitalWrite(LED_PIN_3, LOW);
  digitalWrite(LED_PIN_4, LOW);
}  

void flashLEDs(){
  for(int i=0; i<3; i++){
    digitalWrite(LED_PIN_1, HIGH);
    digitalWrite(LED_PIN_2, HIGH);
    digitalWrite(LED_PIN_3, HIGH);
    digitalWrite(LED_PIN_4, HIGH);
    delay(300);
    digitalWrite(LED_PIN_1, LOW);
    digitalWrite(LED_PIN_2, LOW);
    digitalWrite(LED_PIN_3, LOW);
    digitalWrite(LED_PIN_4, LOW);
    delay(300);
  }  
}

void flashLEDsOnce(){
  digitalWrite(LED_PIN_1, HIGH);
  digitalWrite(LED_PIN_2, HIGH);
  digitalWrite(LED_PIN_3, HIGH);
  digitalWrite(LED_PIN_4, HIGH);
  delay(100);
  digitalWrite(LED_PIN_1, LOW);
  digitalWrite(LED_PIN_2, LOW);
  digitalWrite(LED_PIN_3, LOW);
  digitalWrite(LED_PIN_4, LOW);
}

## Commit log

2015-05-10 added design files
    [10 PORT HEADER.SLDPRT, 102 RESISTOR PACK.SLDPRT, 103 RESISTOR PACK.SLDPRT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]
2015-05-11 added arduino and processing files, mat
2015-05-12 Updated iphone adapter part
    [iphone_6_adapter.SLDPRT, iphone_6_adapter.STL]
2015-05-14 updated laser cut parts
    [3_16_acrylic.dxf, motor_gear.SLDPRT, motor_gear.STL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]
2015-07-06 updated arduino code to fix communication bug
    [hardware_bom.xlsx]
2015-07-17 updated pcb files
2015-07-19 updated spin arduino sketch
2015-07-28 updated arduino sketch for setup configuration in app
2015-09-16 added cs5 compatible dxf files and illustrator files for laser cutting
    [1_8_acrylic.dxf]
2015-10-19 added new arduino sketch for faster spins
2015-11-03 updated board silkscreen to indicate LED directions, 1206 package outlines
    [pcb_bom.xls, spin.brd, spin.sch]
2016-02-12 added modified turntable design for 12-inch laser cutters
    [10 PORT HEADER.SLDPRT, 102 RESISTOR PACK.SLDPRT, 103 RESISTOR PACK.SLDPRT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]
2016-04-04 added modified device dock
    [iphone_dock_2.SLDPRT, iphone_dock_2.STL, iphone_dock_3.SLDPRT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]
2016-04-05 replaced iphone dock with new ios dock
    [ios_dock.SLDPRT, ios_dock.STL, iphone_dock_3.SLDPRT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]
2016-07-27 updated spin arduino code for android app
2016-09-26 edited spin pcb resistor value for android communication
    [pcb_bom.xls, spin.brd, spin.sch]

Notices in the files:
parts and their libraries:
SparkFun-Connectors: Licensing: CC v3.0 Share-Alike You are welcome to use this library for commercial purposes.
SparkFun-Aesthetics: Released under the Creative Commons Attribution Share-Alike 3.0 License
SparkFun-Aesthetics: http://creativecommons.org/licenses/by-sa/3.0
